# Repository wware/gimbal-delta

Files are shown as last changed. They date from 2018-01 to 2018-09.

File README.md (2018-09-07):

# Gimbal delta printer/CNC

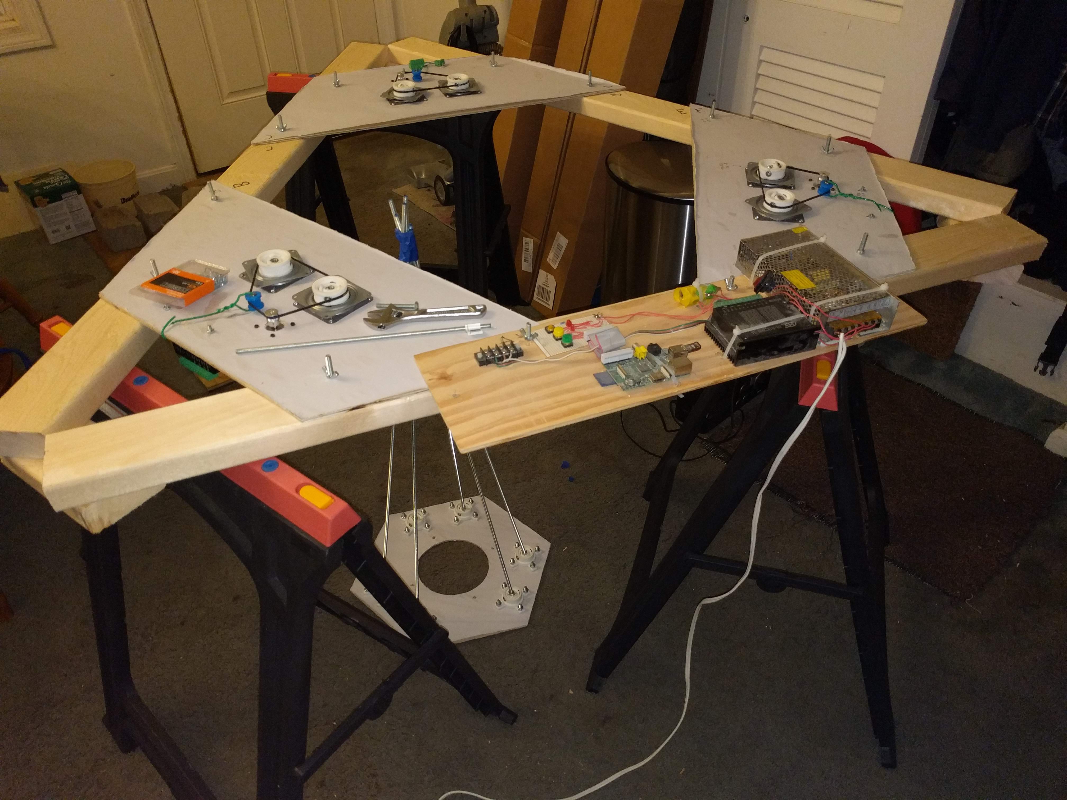
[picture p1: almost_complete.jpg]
Picture of gadget


The fundamental part of the gimbal delta printer is a
[2-axis gimbal](https://github.com/wware/gimbal-delta/blob/master/gimbal1.stl)
holding a nut that takes a 1/4"-20 threaded rod. Each gimbal nut requires
four [684ZZ bearings](https://www.amazon.com/Bearing-684ZZ-4x9-Shielded-4x9x4/dp/B002BBKI7Q).
If you have four gimbal nuts, two mounted to one surface and two mounted
to another, you can have parallel arms as they are used in a
[Rostock delta printer](http://reprap.org/wiki/Delta_geometry) to keep the
tool mount platform horizontal.

So you have
[three pairs of arms](https://github.com/wware/gimbal-delta/blob/master/machine.stl)
like a Rostock, but instead of moving the upper ends of the arms up and down on linear
rails, you shorten and lengthen the three arm pairs. The gimbal nuts on the
tool mount platform are not allowed to rotate, and the threaded rods are epoxied
into their nuts, again to prevent rotation. The gimbal nuts on the printer frame,
at the upper ends of the arm pairs, are driven by a
[GT2 timing belt](http://sdp-si.com/products/timing-belts/gt2.php) to turn in
synchrony, maintaining the parallel-ness of the arm pairs. The belt for each pair
is driven by a stepper motor.

Put a reasonably flexible connector on the tool mount platform, and it will accommodate
a [router](https://www.amazon.com/Routers/b/ref=dp_bc_4?ie=UTF8&node=552866) or an
[extruder](https://www.matterhackers.com/store/c/HotEnds) or a laser engraver, or maybe
just a marker for plotting.

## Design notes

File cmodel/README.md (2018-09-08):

# Calibration model

This is a mathematical model for calibrating the gimbal delta machine. The hope is to get fairly
high positional precision, hopefully a millimeter or better.

The pairs of threaded rods can be modeled as two points, and one of those points can be the tooltip.
Applying that to all three pairs, we have an inverted tetrahedron whose lower vertex is the tooltip.
The calibration process involves using some kind of least-squares method to find the other three
vertices and the lengths of the edges connecting them to the tooltip vertex.

Logistically, the procedure is to begin with approximate values for all these things that are good
enough to move the tooltip around in predictable directions and distances, and then lower the tooltip
onto several points on a flat surface. The locations of those points are known. Using that knowledge
and the controls we used to position the tooltip, we should be able to figure out more accurate
values.

We want to find three lengths and three points, or a total of 12 scalars, so we'll need at least 12
points on our reference surface.

Let's assume that we have nominal rod lengths and our controls are deltas from those nominal lengths.
Let those lengths be La, Lb, and Lc, and the tops of those rods are the points (xa, ya, za),
(xb, yb, zb), and (xc, yc, zc) respectively. The length deltas can be Da, Db, and Dc.

The forward kinematics problem is to map (Da, Db, Dc) to the position of the tooltip (x, y, z). The
inverse kinematics problem is to map (x, y, z) to (Da, Db, Dc). Surprisingly, the inverse kinematics
problem is easier to solve.

    # Given all our parameters...
    X = np.array((x, y, z))
    A = np.array((xa, ya, za))
    B = np.array((xb, yb, zb))
    C = np.array((xc, yc, zc))
    Da = linalg.norm(A - X) - La
    Db = linalg.norm(B - X) - Lb
    Dc = linalg.norm(C - X) - Lc

To solve the forward kinematics problem, we need to specify (Da, Db, Dc) and then find the vector
X representing the intersection of three spheres. This is [a solved problem](https://stackoverflow.com/questions/1406375).
Given the function defined in the last Stack Overflow answer, we can write

    x, y, z = trilaterate(A, B, C, La + Da, Lb + Db, Lc + Dc)

Gee, that was easier than I expected. OK, on to formulating the least-squares method.

Recognize that the values we have for A, B, C, La, Lb, Lc are approximations of values that are
correct but unknown. So we have *our* answer and *the right* answer.

    X~ = F(Da, Db, Dc, A~, B~, C~, La~, Lb~, Lc~)     # parameters known but approximate
    X = F(Da, Db, Dc, A, B, C, La, Lb, Lc)            # paramaters unknown but correct

So set up a square error figure, summed over several (X, D) pairs.

    ErrSq = sum([linalg.norm(X - X~) ** 2 for D in manyDs])
    partial d(ErrSq)/d(param) = 2 * sum([linalg.norm(X - X~) * (dX/dparam) for D in manyDs])

It won't be practical to find a closed form for dX/dparam, so I'll need to iterate a Newton's
method or conjugate-gradient thingy or whatever to solve this. So you have a vector of partial
derivatives

    (dX/dLa, dX/dLb, dX/dLc, dX/dxa, dX/dya, dX/dza, dX/dxb... dX/dzc)

defined for any point in the twelve-space, and you take your D vectors corresponding to the
known reference X points, and you

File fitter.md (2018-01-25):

# What I learned from the fitter piece

The step of 0.25 mm turns out to be too large. The outer dimension
of 9 mm is a bit too snug, but 9.25 mm is way too loose. My guess is
that 9.1 mm might be just right. I think a better step would be 0.05 mm.

Also, there is little need for smaller-than-9-mm sizes. One would be
fine. So my next plan is something like this.

    module ThirdPiece() {
        difference() {
            intersection() {
                ...
            }
            for (n = [-1 : 3])    // note different for-loop limits
                rotate([0, 0, n * 60])
                    rotate([90, 0, 0])
                        translate([0, 0, 0])
                            cylinder(h=60, d=9 + 0.05*n);   // 0.05 mm step
        }
        for (n = [-1 : 3])
            rotate([0, 0, 180 - 30 + n * 60])
                translate([0, R3+5, 0])
                    rotate([-90, 0, 0]) nub(4 + 0.05*n);
    }

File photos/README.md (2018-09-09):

# Photos of the gimbal delta printer/CNC

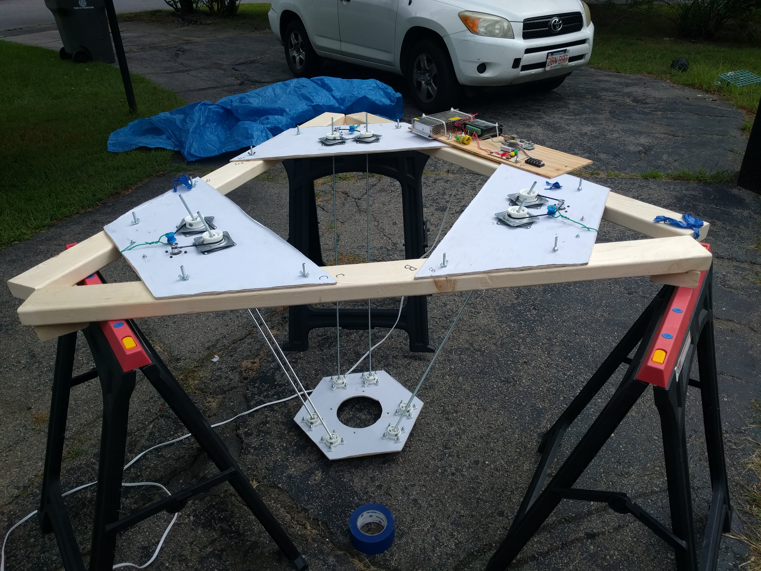
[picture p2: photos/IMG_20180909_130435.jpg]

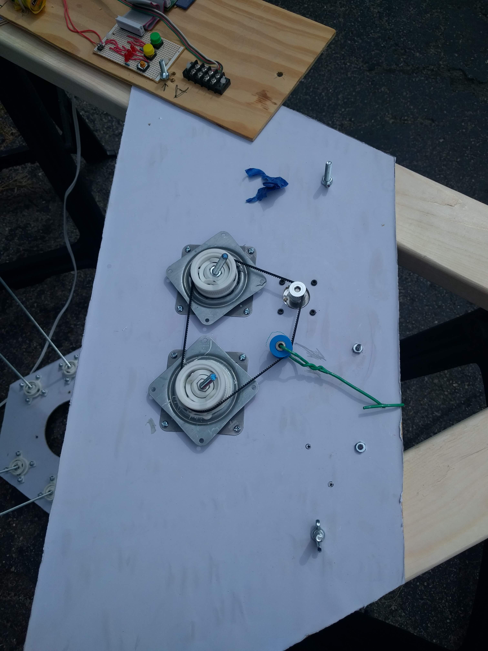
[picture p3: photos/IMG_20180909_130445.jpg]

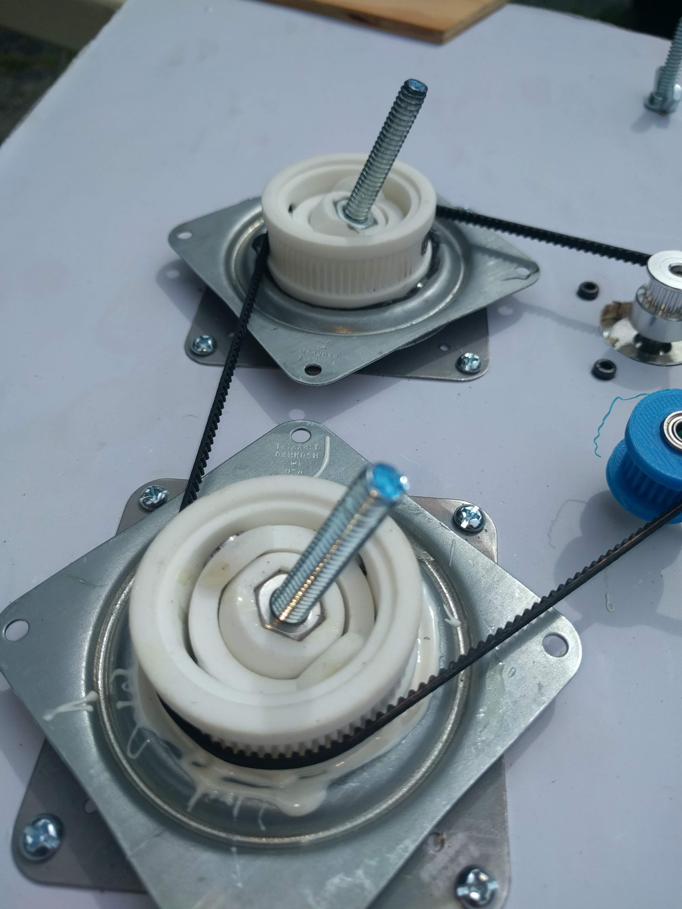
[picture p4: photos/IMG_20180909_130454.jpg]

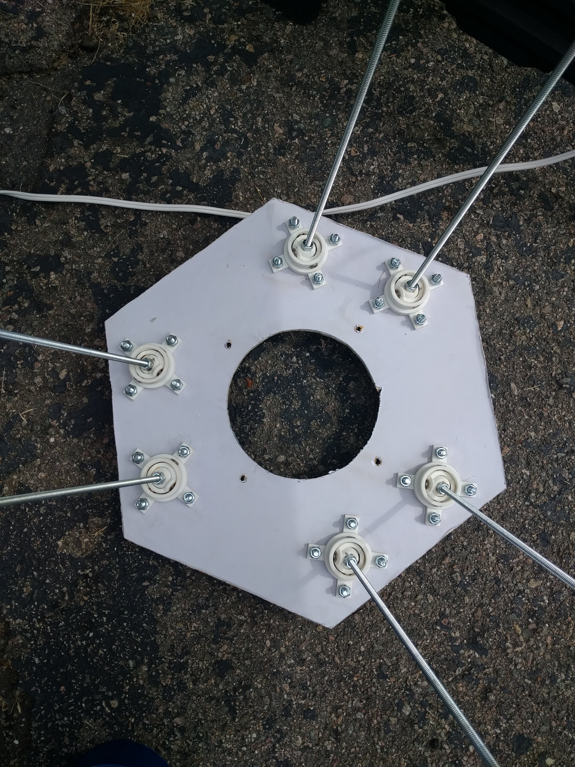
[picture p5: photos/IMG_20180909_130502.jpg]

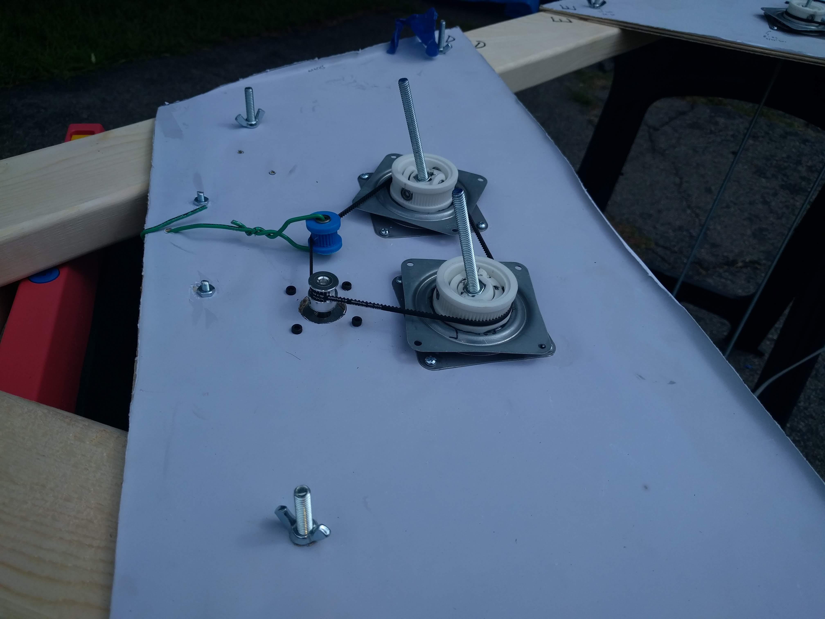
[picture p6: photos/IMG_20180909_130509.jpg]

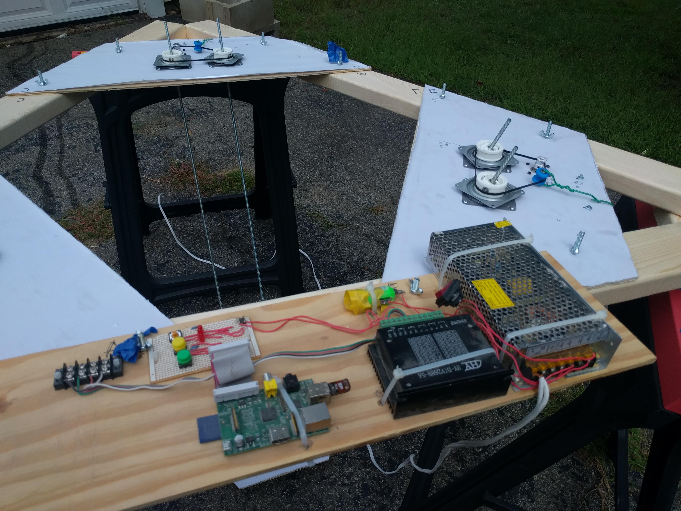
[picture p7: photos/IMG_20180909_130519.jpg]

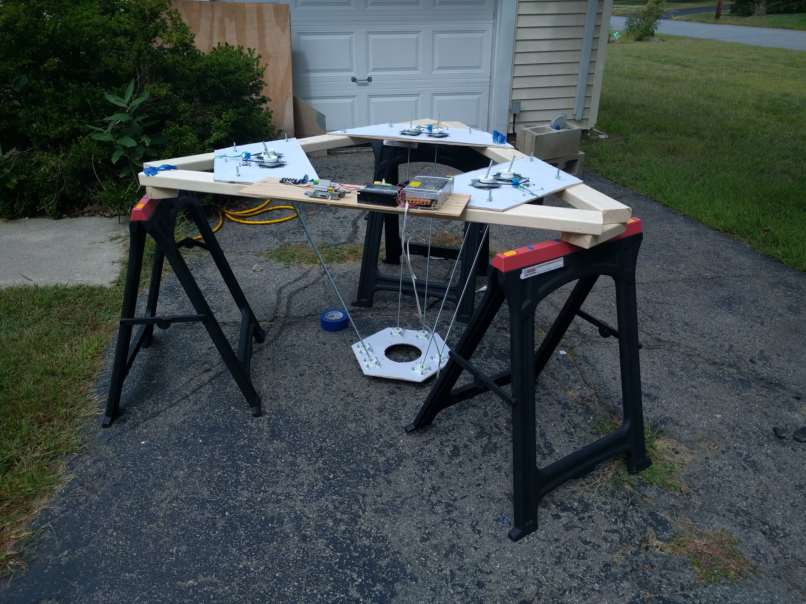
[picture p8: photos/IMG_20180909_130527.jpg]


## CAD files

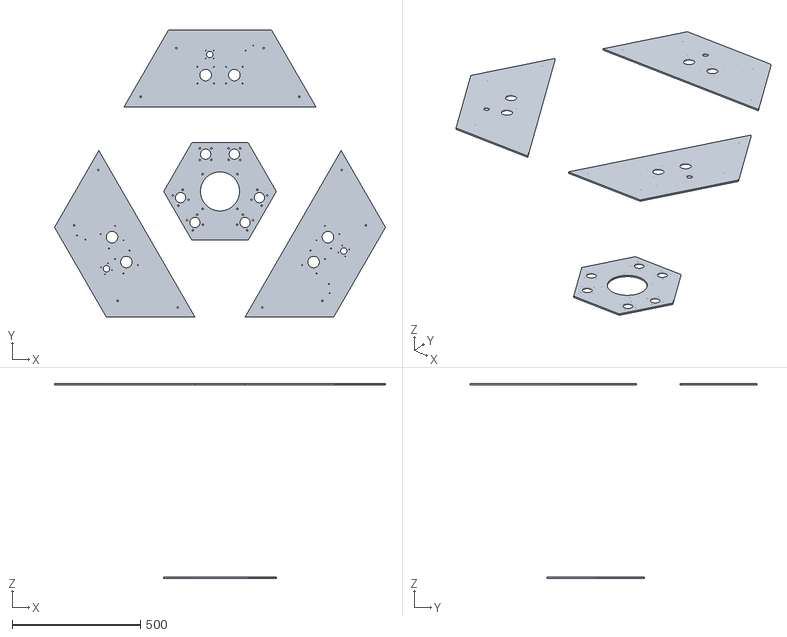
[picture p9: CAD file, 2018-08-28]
machine.stl
1292.8 x 1119.6 x 762.0

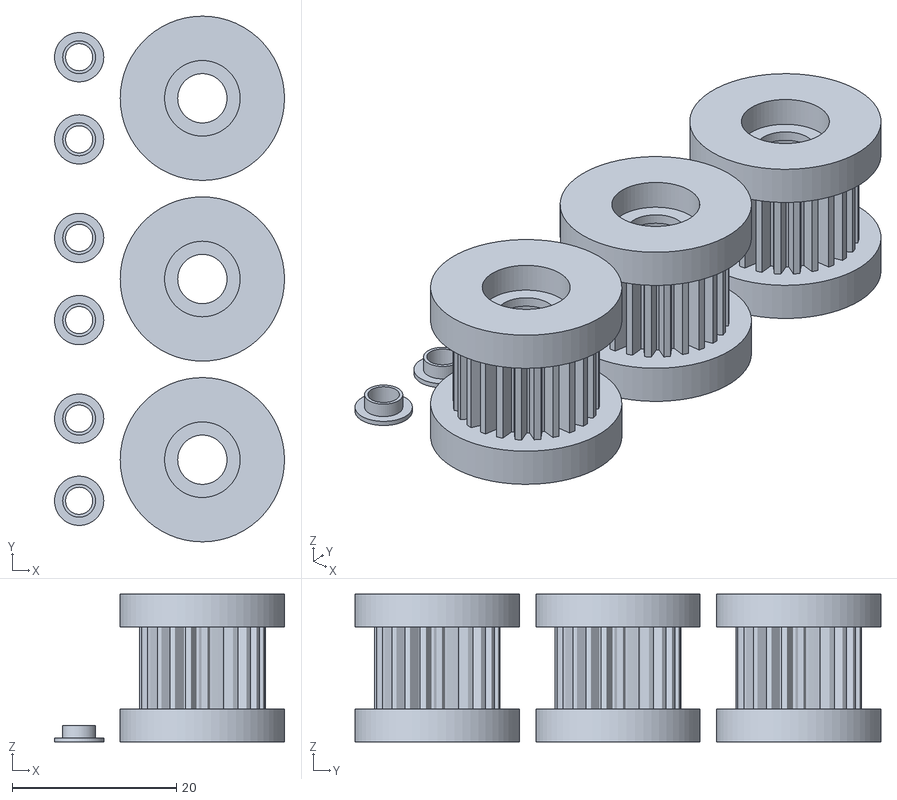
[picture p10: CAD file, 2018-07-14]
tensioner_pieces.stl
28.0 x 64.0 x 18.0

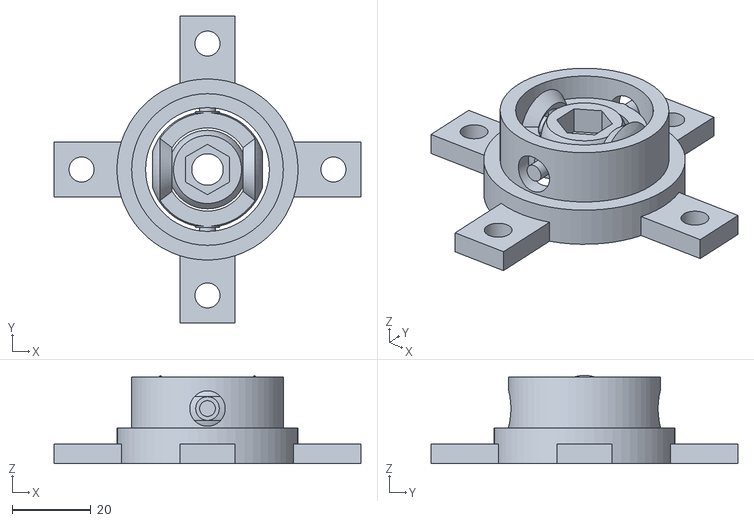
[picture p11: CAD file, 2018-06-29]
fixed_gimbal.stl
78.0 x 78.0 x 22.4

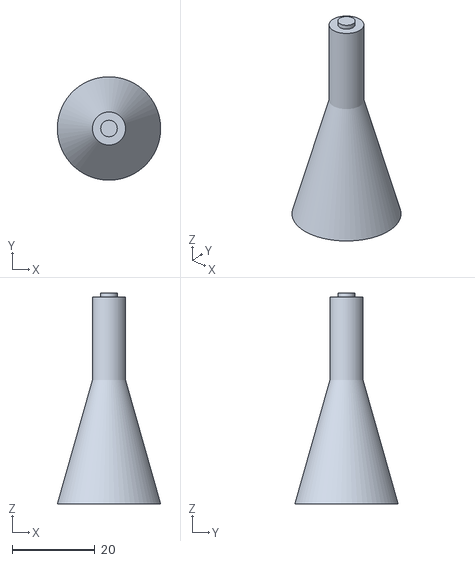
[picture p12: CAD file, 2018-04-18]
tool.stl
25.0 x 25.0 x 51.0

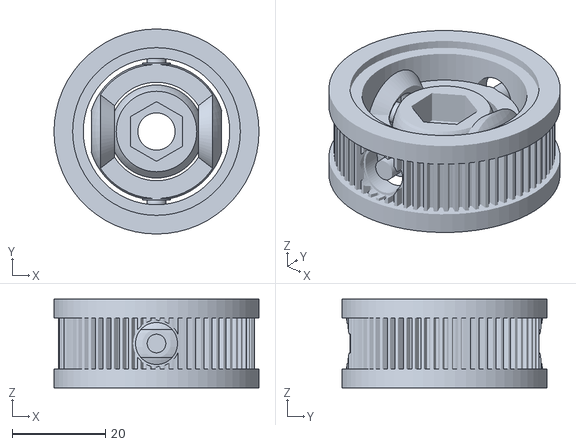
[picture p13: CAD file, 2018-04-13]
rotor.stl
44.0 x 44.0 x 19.0

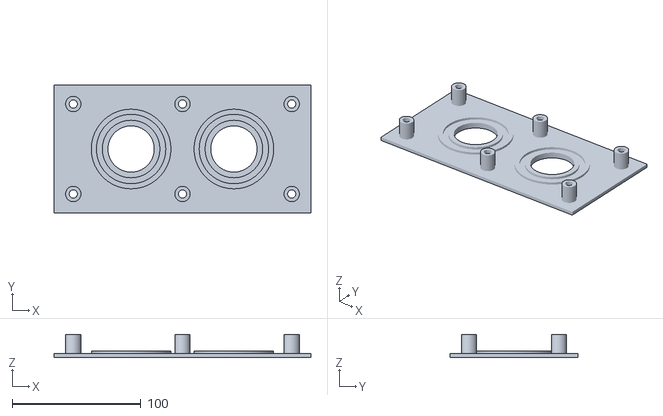
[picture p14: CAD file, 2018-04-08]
baseplate.stl
200.0 x 100.0 x 18.0

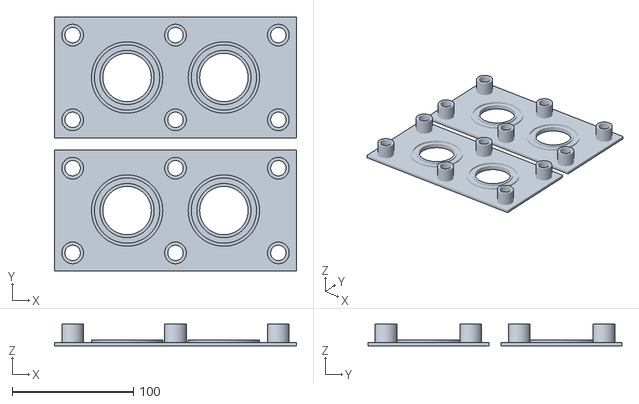
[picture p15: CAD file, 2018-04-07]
two_baseplates.stl
200.0 x 210.0 x 18.0

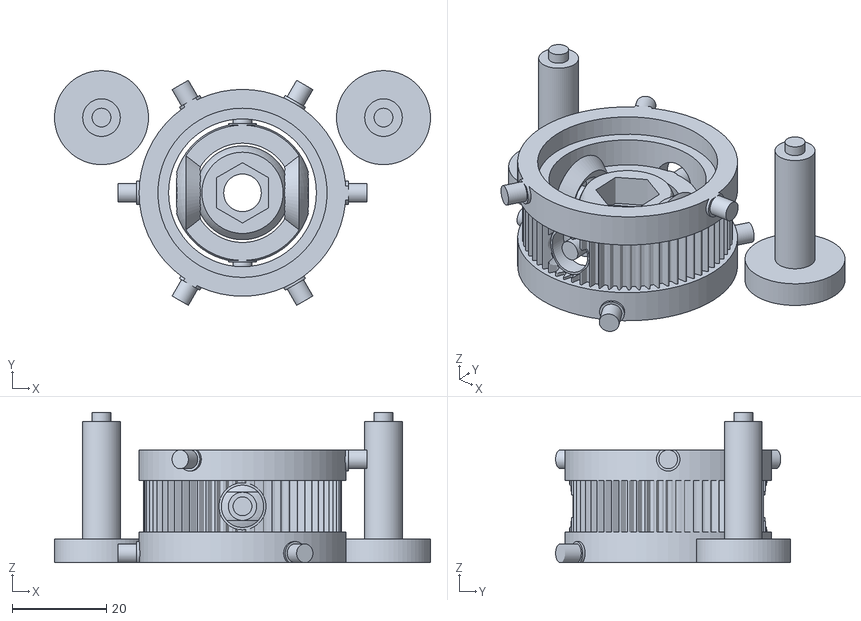
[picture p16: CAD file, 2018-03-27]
rotor2.stl
80.0 x 49.9 x 32.0

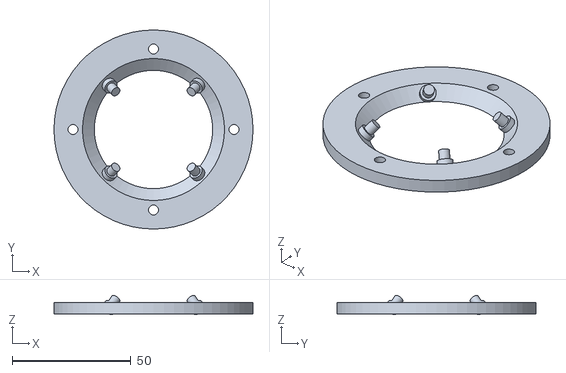
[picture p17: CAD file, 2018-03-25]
altbaseplate.stl
83.8 x 83.8 x 8.07

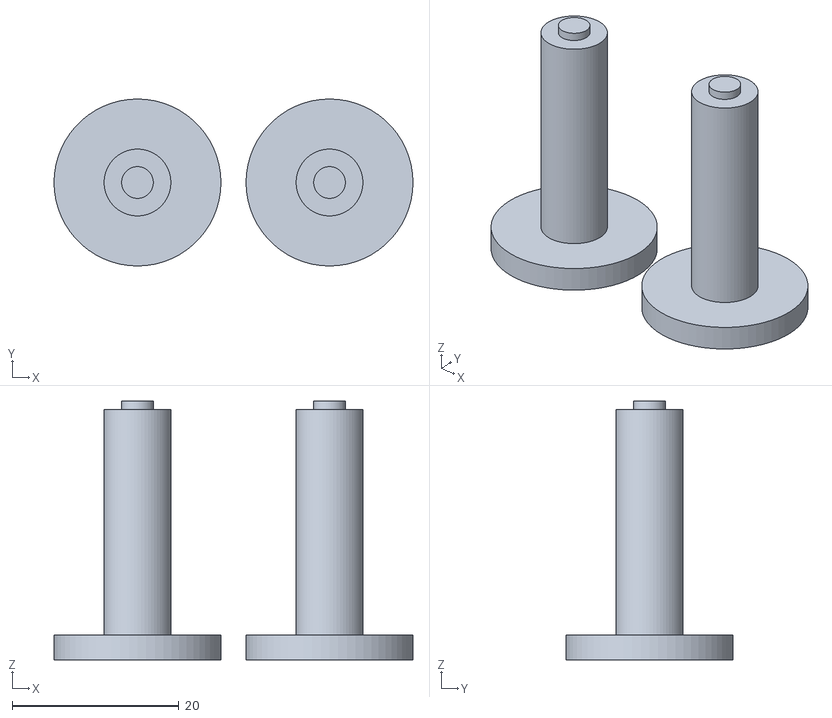
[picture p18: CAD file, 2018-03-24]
bearing_tool.stl
43.0 x 20.0 x 31.0

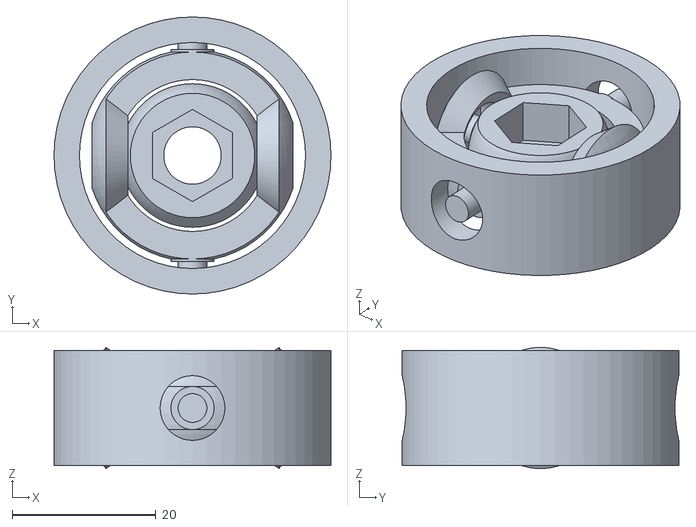
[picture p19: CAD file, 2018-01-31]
gimbal1.stl
38.5 x 38.5 x 16.9

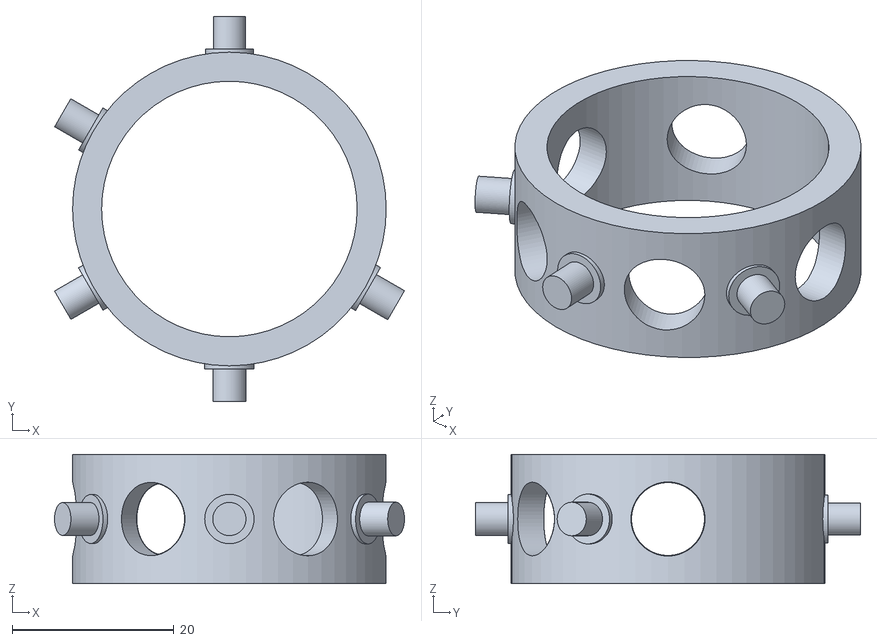
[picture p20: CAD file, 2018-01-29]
fitter.stl
43.2 x 47.6 x 16.0

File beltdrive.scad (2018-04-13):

// $fn = 60;
pi = 3.1415926;

pitch = 2;   // 2GT timing belt

a = 0.4;

module tooth(h) {
    M1 = [[ 1  , a , 0  , 0   ],
           [ 0  , 2 , 0  , 0   ],
           [ 0  , 0 , 1  , 0   ],
           [ 0  , 0 , 0  , 1   ] ] ;
    M2 = [[ 1  , -a , 0  , 0   ],
           [ 0  , 2  , 0  , 0   ],
           [ 0  , 0  , 1  , 0   ],
           [ 0  , 0  , 0  , 1   ] ] ;
    translate([-1, -0.5, -h/2])
        intersection() {
            multmatrix(M1) {
                cube(size=[1.5,1,h]);
            }
            multmatrix(M2) {
                cube(size=[1.5,1,h]);
            }
        }
}

module beltdrive(N, h, w) {
    b = 0.6;
    r = (1 / sin(180 / N)) - 1.5;
    echo(r);
    echo(r-w);
    difference() {
        translate([0, 0, -h/2])
            cylinder(r=r, h=h);
        translate([0, 0, -h/2-1])
            cylinder(r=r-w, h=h+2);
    }
    for (i = [0 : N-1]) {
        rotate(i * 360 / N, [0, 0, 1])
            translate([0, r, 0])
                tooth(h);
    }
}

/* To avoid a "wall too thin" warning from Shapeways, you need the
   outer edge of the tooth to be at least 0.7 mm thick. This requires
   dropping the value of a to 0.4.
 */

// beltdrive(62, 3, 0.6);
// tooth(3);
// translate([-0.6, 1.5, 0]) cube([0.7, 1, 1]);

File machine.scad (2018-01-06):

$fn = 30;
INCH = 25.4;

arm_separation = 70;
driver_width = arm_separation + 60;

// http://reprap.org/wiki/NEMA_17_Stepper_motor
nema17height = 50;    // approximate
nema17width = 42.3;

module GimbalNut() {
    translate([0, 0, -0.01])
        cylinder(r=19.2, h=16);
}

module GimbalNutPair() {
    translate([-.5 * arm_separation, 0, 0])
        GimbalNut();
    translate([.5 * arm_separation, 0, 0])
        GimbalNut();
}

module dewalt660router() {
    // http://www.dewalt.com/products/power-tools/cutout-tools/cutout-tool/dw660
    cylinder(d=3*INCH, h=10*INCH);
    translate([0, 0, -25])
        cylinder(d=15, h=30);
}

hex_diameter = 150;

module ToolMountPlatform() {
    dewalt660router();
    // plywood hexagon
    translate([0, 0, -5])
        linear_extrude(height=5)
            circle(hex_diameter, $fn=6);
    // 3 pairs of gimbal nuts
    for (n = [1 : 3])
        rotate(120 * n, [0, 0, 1])
            translate([0, 100, 0])
                GimbalNutPair();
}

ToolMountPlatform();

module DriverModule() {
    GimbalNutPair();
    // plywood
    translate([-.5*driver_width, -25, -5])
        cube([driver_width, 110, 5]);
    // stepper motor
    translate([-.5*nema17width,
              50 - .5*nema17width,
              -nema17height - 5])
        cube([nema17width, nema17width, nema17height]);
    // stepper motor shaft
    translate([0, 50, 0])
        cylinder(d=0.4*INCH, h=24);
}

// there needs to be a frame to hold the 3 driver modules
for (n = [1 : 3])
    rotate(120 * n, [0, 0, 1])
        translate([0, 380, 600])
            DriverModule();

// threaded rods connecting driver modules to tool mount
for (n = [1 : 3])
    rotate(120 * n, [0, 0, 1])
        for (m = [0 : 1])
            translate([(m - .5) * arm_separation, 100, 8]) {
                rotate(-25, [1, 0, 0])
                    cylinder(d=5, h=36*INCH);
            }

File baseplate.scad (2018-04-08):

$fn=60;

include <gimbal1.scad>;
include <beltdrive.scad>;

GIMBAL_OUTER_DIAMETER = 2 * R5;
GIMBAL_HEIGHT =  thirdHeight;
RING_OFFSET = 4.7;

module gimbal_outline() {
    translate([0, 0, -.5 * GIMBAL_HEIGHT])
    cylinder(d=GIMBAL_OUTER_DIAMETER, h=GIMBAL_HEIGHT);
}

module bearing_684zz() {
    difference() {
        translate([0, 0, -2]) cylinder(h=4, d=9);
        translate([0, 0, -3]) cylinder(h=6, d=4);
    }
}

module bearing_608zz() {
    difference() {
        translate([0, 0, -3.5]) cylinder(h=7, d=22);
        translate([0, 0, -4]) cylinder(h=8, d=8);
    }
}

module bearings() {
    // 6.5 = (9 + 4) / 2, from the bearing
    C = 6.5 / sqrt(2);
    for (i = [0 : 2]) {
        a = 0.5 * GIMBAL_OUTER_DIAMETER + C;
        b = C + RING_OFFSET;
        rotate(30 + 120*i, [0, 0, 1]) {
            translate([a, 0, -b]) rotate(45, [0, 1, 0])
                bearing_684zz();
            translate([a, 0, b]) rotate(45, [0, -1, 0])
                bearing_684zz();
        }
    }
}

module half_shell() {
    w = 23.9;
    intersection() {
        for (j = [0 : 3]) {
            rotate((j+.25)*90, [0, 0, 1])
            translate([w, 0, 0])
                rotate(45, [0, -1, 0]) {
                    h1 = 4;
                    h2 = 2.4;
                    %bearing_684zz();
                    translate([0, 0, -2-0.01])
                        cylinder(d=4, h=4+0.02);
                    translate([0, 0, -(h2+2)])
                        cylinder(d=6, h=h2);
                };
        };
    };
    h = 5;
    difference() {
        k = 12;
        translate([0, 0, -5.1+.01])
            cylinder(r=w+1+k+h, h=h-0.02);
        translate([0, 0, -5.1])
            cylinder(r=w+1+h, h=h);
        for (i = [0 : 3]) {
            rotate(i * 90, [0, 0, 1])
                translate([w+10, 0, -100])
                    // 8-32 machine screw
                    cylinder(d=0.164*25.4, h=200);
        }
    };
    difference() {
        translate([0, 0, -5.1+.01])
            cylinder(r=w+1+h, h=h-0.02);
        translate([0, 0, -5.1])
            cylinder(r1=w+1, r2=w+1+h, h=h);
    };
};


module post() {
    extra = 2;
    translate([0, 0, -(2+extra)]) {
        cylinder(d=4, h=4+extra);
        cylinder(d=5, h=extra);
    };
    %bearing_684zz();
};

module post_pair() {
    C = 6.5 / sqrt(2);
    a = 0.5 * GIMBAL_OUTER_DIAMETER + C;
    b = C + RING_OFFSET;
    for (j = [0 : 1]) {
        rotate(j*180, [1, 0, 0])
            translate([0, 0, b]) rotate(45, [0, -1, 0]) {
                translate([0, 0, -6]) cylinder(d=4, h=8);
                translate([0, 0, -6]) cylinder(d=5, h=4);
            }
    }
    translate([-2.5, 0, 0])
        intersection() {
            rotate(45, [0, 1, 0])
                translate([0, -5, 0])
                    cube([20, 10, 12]);
            translate([3.5, -50, -50])
                cube(100, 100, 100);
        }
    translate([7, -5, -15])
        cube([20, 10, 10]);
}

module flat_head_screw_cutout(D, H, L) {
    // https://tinyurl.com/ybmmaz7t - dimensions
    D = 3; H = 1.7; L = 10;  // M3
    translate([0, 0, -(D+H)/2])
        cylinder(d1=0, d2=D+H+2, h=(D+H)/2+1);
    translate([0, 0, -L])
        cylinder(d=D, h=L);
};

module m3_cutout(L) { flat_head_screw_cutout(3, 1.7, L); };
module m4_cutout(L) { flat_head_screw_cutout(4, 2.3, L); };
module m5_cutout(L) { flat_head_screw_cutout(5, 2.8, L); };
module m6_cutout(L) { flat_head_screw_cutout(6, 3.3, L); };

module posts() {
    C = 6.5 / sqrt(2);
    a = 0.5 * GIMBAL_OUTER_DIAMETER + C;
    for (i = [0 : 2])
        rotate(30 + 120*i, [0, 0, 1])
            translate([a, 0, 0])
                post_pair();
    translate([0, 0, -19.99])
    difference() {
        cylinder(h=5, d=103);
        union() {
            translate([0, 0, -1])
                cylinder(h=7, d=65);
            translate([-125, -15, -1])
                cube([250, 1, 7]);
            translate([33, -28, 5])
                m5_cutout(15);
            translate([-33, -28, 5])
                m5_cutout(15);
            translate([42, -3, 5])
                m5_cutout(15);
            translate([-42, -3, 5])
                m5_cutout(15);
            translate([15, 42.5, 5])
                m5_cutout(15);
            translate([-15, 42.5, 5])
                m5_cutout(15);
        };
    };
}

module cylinder_ring(inner, middle, outer) {
    difference() {
        cylinder(d1=outer, d2=middle, h=0.5*(outer-middle));
        translate([0, 0, -1])
        cylinder(d=inner, h=(2+outer-middle));
    }
}

module with_rings() {
    D = 4 * sqrt(2);
    translate([0, 0, RING_OFFSET])
    cylinder_ring(GIMBAL_OUTER_DIAMETER - 0.1,
        GIMBAL_OUTER_DIAMETER,
        GIMBAL_OUTER_DIAMETER + D);

    translate([0, 0, -RING_OFFSET])
    rotate(180, [1, 0, 0])
    cylinder_ring(GIMBAL_OUTER_DIAMETER - 0.1,
        GIMBAL_OUTER_DIAMETER,
        GIMBAL_OUTER_DIAMETER + D);
}

module ring_with_posts(offset) {
    width = 36;
    thickness = 4;
    height = 6.5;
    translate([0, 0, -2])
    difference() {
        cylinder(d=width+2*thickness, h=height);
        translate([0, 0, -0.01])
        cylinder(d=width, h=height+0.02);
    };
    for (i = [0 : 2]) {
        rotate((i+offset)*120, [0,0,1])
            translate([width/2+thickness+2.5, 0, height-4])
            rotate(90, [0,1,0]) post();
    };
};

module full_rotor() {
    a = 7.5;
    intersection() {
        union() {
            translate([0, 0, a])
                ring_with_posts(0);
            translate([0, 0, -a])
                mirror([0,0,1])
                ring_with_posts(1/2);
        };
        translate([0, 0, -12])
            cylinder(h=24, d=100);
    };
    GimbalNut();
    difference() {
        translate([0, 0, -0.05])
        beltdrive(66, 12.1, 0.6);
        rotate(90, [1, 0, 0])
            translate([0, 0, -25])
                cylinder(h=50, d=10);
    }
}

module rotor_cross_section() {
    intersection() {
        full_rotor();
        translate([-500, -500, -1000])
            cube([1000, 1000, 1000]);
    }
}

module all_posts() {
    gap = 85;
    translate([0, -gap/2, 0]) posts();
    translate([0, gap/2, 0]) mirror([0, 1, 0]) posts();
};

module bearing_tool() {
    W = 20;
    L = 30;
    gap = 3;
    cylinder(h=5, d=W);
    cylinder(h=L+2, d=4);
    cylinder(h=L, d=8);
};

if (0) {
    gap = 85;
    %translate([0, -gap/2, 0]) full_rotor();
    %translate([0, -gap/2, 0]) bearings();
    %translate([0, gap/2, 0]) full_rotor();
    %translate([0, gap/2, 0]) mirror([0, 1, 0]) bearings();
    all_posts();
}
if (0) {
    // post_pair();
    half_shell();
    %translate([0, 0, -9.3]) full_rotor();
    translate([0, 0, -18.55])
        rotate(180, [0, 1, 0])
            half_shell();
}
if (0) {
    p = 25;
    full_rotor();
    if (0) {
        %cylinder(r1=0, r2=p, h=p);
        %rotate(180, [1,0,0]) cylinder(r1=0, r2=p, h=p);
    }/*
    translate([30, 16, -12])
        bearing_tool();
    translate([-30, 16, -12])
        bearing_tool();*/
}
//post();

module track() {
    difference() {
        translate([0, 0, -1]) cylinder(h=3, r=31);
        translate([0, 0, -1.1]) cylinder(h=3.2, r=27);
    };
    difference() {
        translate([0, 0, -1]) cylinder(h=3, r=22.4);
        translate([0, 0, -1.1]) cylinder(h=3.2, r=18);
    };
};

module baseplate() {
    a = 40;
    u = 85;
    v = 35;
    translate([-a, 0, 0]) track();
    translate([a, 0, 0]) track();
    difference() {
        translate([-100, -50, -3])
            cube([200, 100, 3]);
        translate([-a, 0, -5])
            cylinder(r=18, h=10);
        translate([a, 0, -5])
            cylinder(r=18, h=10);
        for (i = [0 : 1]) {
            for (j = [0 : 1]) {
                translate([(2*i-1) * u, (2*j-1) * v, 0]) {
                    translate([0, 0, -5])
                        cylinder(d=6.35, h=10);
                };
            };
        };
        for (j = [0 : 1]) {
            translate([0, (2*j-1) * v, 0]) {
                translate([0, 0, -5])
                    cylinder(d=6.35, h=10);
            };
        };
    };
    for (i = [0 : 1]) {
        for (j = [0 : 1]) {
            translate([(2*i-1) * u, (2*j-1) * v, 0]) {
                difference() {
                    cylinder(d=12, h=15);
                    translate([0, 0, -0.1])
                        cylinder(d=6.35, h=15.2);
                };
            };
        };
    };
    for (j = [0 : 1]) {
        translate([0, (2*j-1) * v, 0]) {
            difference() {
                cylinder(d=12, h=15);
                translate([0, 0, -0.1])
                    cylinder(d=6.35, h=15.2);
            };
        };
    };
};

if (0) {
    translate([0, 0, -15]) {
        %translate([40, 0, 15.5]) {
            full_rotor();
        };
        %translate([-40, 0, 15.5]) {
            full_rotor();
        };
        baseplate();
        translate([0, 0, 30])
            rotate(180, [1, 0, 0])
                baseplate();
    };
}

baseplate();

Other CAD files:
bearing_tool.scad
fitter.scad
gimbal1.scad
rotor.scad
tool.scad

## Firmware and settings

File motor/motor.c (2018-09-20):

#include <unistd.h>
#include <stdlib.h>
#include <stdio.h>
#include <time.h>
#ifdef RASPBERRY_PI
#include <bcm2835.h>
#else
#include "sim_bcm2835.h"
#endif

#define PULA    21
#define DIRA    20
#define ENAA    16

#define PULB    13
#define DIRB    19
#define ENAB    26

#define PULC    12
#define DIRC    25
#define ENAC    24

#define MAX(x,y)  (((x) > (y)) ? (x) : (y))
#define ABS(x)    MAX(x, -(x))

#define MODULO   100000

// PERIOD is in nanoseconds
#define PERIOD   100000L

struct pinstruct {
    int phase;
    int state;
    int pin;
};

static struct pinstruct astruct = { 0, 0, PULA };
static struct pinstruct bstruct = { 0, 0, PULB };
static struct pinstruct cstruct = { 0, 0, PULC };
static int init_done = 0;

void process_pin(struct pinstruct *pstr, int value)
{
    pstr->phase += value;
    if (pstr->phase > MODULO) {
        bcm2835_gpio_write(pstr->pin, pstr->state ? HIGH : LOW);
        pstr->state = !pstr->state;
        pstr->phase %= MODULO;
    }
}

int run_motors(int avalue, int bvalue, int cvalue, int usecs, int enable_debug)
{
    int iter;
    struct timespec ts = {0};

    ts.tv_sec = 0;
    ts.tv_nsec = PERIOD;

    if (enable_debug)
        bcm2835_set_debug(1);

    if (!init_done) {
        if (!bcm2835_init())
            return 1;
        init_done = 1;
    }

    bcm2835_gpio_fsel(PULA, BCM2835_GPIO_FSEL_OUTP);
    bcm2835_gpio_fsel(DIRA, BCM2835_GPIO_FSEL_OUTP);
    bcm2835_gpio_fsel(ENAA, BCM2835_GPIO_FSEL_OUTP);

    bcm2835_gpio_fsel(PULB, BCM2835_GPIO_FSEL_OUTP);
    bcm2835_gpio_fsel(DIRB, BCM2835_GPIO_FSEL_OUTP);
    bcm2835_gpio_fsel(ENAB, BCM2835_GPIO_FSEL_OUTP);

    bcm2835_gpio_fsel(PULC, BCM2835_GPIO_FSEL_OUTP);
    bcm2835_gpio_fsel(DIRC, BCM2835_GPIO_FSEL_OUTP);
    bcm2835_gpio_fsel(ENAC, BCM2835_GPIO_FSEL_OUTP);

    bcm2835_gpio_write(ENAA, HIGH);
    bcm2835_gpio_write(DIRA, (avalue < 0) ? HIGH : LOW);
    avalue = ABS(avalue);

    bcm2835_gpio_write(ENAB, HIGH);
    bcm2835_gpio_write(DIRB, (bvalue < 0) ? HIGH : LOW);
    bvalue = ABS(bvalue);

    bcm2835_gpio_write(ENAC, HIGH);
    bcm2835_gpio_write(DIRC, (cvalue < 0) ? HIGH : LOW);
    cvalue = ABS(cvalue);

    for (iter = 0; iter < usecs; iter++) {
        if (enable_debug)
            printf("%d %d %d %d\n", iter, astruct.phase, bstruct.phase, cstruct.phase);
	process_pin(&astruct, avalue);
	process_pin(&bstruct, bvalue);
	process_pin(&cstruct, cvalue);
        nanosleep(&ts, (struct timespec *) NULL);
    }

    bcm2835_gpio_write(ENAA, LOW);
    bcm2835_gpio_write(ENAB, LOW);
    bcm2835_gpio_write(ENAC, LOW);

    return 0;
}

#ifdef MOTORMAIN
const char *helpstring = "MODULO=%d PERIOD=%d\n"
"  Example usage: %s -D 10000 -c 45000\n"
"Command line options\n"
"    -a <n>   rate multiple of the A motor, positive up, negative down\n"
"    -b <n>   rate multiple of the B motor, positive up, negative down\n"
"    -c <n>   rate multiple of the C motor, positive up, negative down\n"
"    -D <n>   duration\n"
"    -h,-?    help\n";

int main(int argc, char **argv)
{
    int c, debugflag = 0, duration = 300;
    int avalue = 0, bvalue = 0, cvalue = 0;

    while ((c = getopt (argc, argv, "?ha:b:c:D:d")) != -1)
        switch (c) {
            case 'h':
            case '?':
                printf(helpstring, MODULO, PERIOD, argv[0]);
                return 0;
            case 'a':
                avalue = atoi(optarg);
                break;
            case 'b':
                bvalue = atoi(optarg);
                break;
            case 'c':
                cvalue = atoi(optarg);
                break;
            case 'D':
                duration = atoi(optarg);
                break;
            case 'd':
                debugflag = 1;
                break;
            default:
                abort();
        }

    return run_motors(avalue, bvalue, cvalue, duration, debugflag);
}
#endif

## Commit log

2018-01-04 an STL file
    [gimbal1.stl]
2018-01-04 Better range of motion
    [gimbal1.scad, gimbal1.stl]
2018-01-04 The entire machine in outline.
    [machine.scad, machine.stl]
2018-01-05 Corrections in machine overview
    [machine.scad, machine.stl]
2018-01-06 more realistic sizing
    [machine.scad, machine.stl]
2018-01-09 Clean up gimbal design, bump up wiggle room.
    [gimbal1.scad, gimbal1.stl]
2018-01-17 Different sizes to fit the bearing.
    [fitter.scad, fitter.stl]
2018-01-29 A better fitter piece.
    [fitter.scad, fitter.stl]
2018-01-31 Try an outer diameter of 9.1 mm, inner 4 mm
    [gimbal1.scad, gimbal1.stl]
2018-02-02 Rotor for driving a gimbal nut.
    [rotor.scad, rotor.stl]
2018-02-13 Rework the rotor.
    [rotor.scad, rotor.stl]
2018-02-24 Add a beltdrive
    [beltdrive.scad]
2018-02-24 Put a bunch of pieces together.
    [beltdrive.scad, rotor.scad]
2018-03-06 Redesign the timing belt teeth.
    [beltdrive.scad, gimbal1.scad, rotor.scad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]
2018-03-06 Try to fix Shapeways walls-too-thin warning.
    [beltdrive.scad, rotor.stl]
2018-03-24 Bearing insertion tool
    [bearing_tool.scad, bearing_tool.stl]
2018-03-24 Baseplate and stl
    [baseplate.stl, rotor.scad]
2018-03-25 Alternative to baseplate with STL
    [altbaseplate.stl, rotor.scad]
2018-03-25 Try four bearings to support, with STL
    [altbaseplate.stl, rotor.scad]
2018-03-26 new rotor design
    [rotor.scad]
2018-03-27 more work
    [rotor.scad, rotor2.stl]
2018-04-07 Baseplates with circular tracks
    [baseplate.scad, two_baseplates.stl]
2018-04-07 more baseplate work
    [baseplate.scad, baseplate.stl]
2018-04-08 diameter not radius
    [baseplate.scad, baseplate.stl]
2018-04-08 Use a lazy susan bearing (https://amzn.to/2JtA3F3)
    [rotor.scad]
2018-04-13 Fix wall-too-thin warning from Shapeways.
    [beltdrive.scad, rotor.scad, rotor.stl]
2018-04-18 Better insertion tool, I hope.
    [tool.scad, tool.stl]
2018-06-05 here's a driver design (start of one), and move rotor up a little
    [driver.scad, rotor.scad]
2018-06-29 the fixed gimbal design
    [fixed_gimbal.stl, rotor.scad]
2018-06-29 replace driver.scad with better
    [driver.scad, rotor.scad]
2018-06-29 Add a STL file for the driver module.
2018-07-06 more work on driver module
    [rotor.scad]
2018-07-10 more tensioner work
    [rotor.scad]
2018-07-26 Lots of progress
    [rotor.scad]
2018-07-26 simplify a bit
    [rotor.scad]
2018-07-26 more simplifications
    [rotor.scad]
2018-07-27 Generate SVG for PDF for plywood.
    [rotor.scad]
2018-08-19 Make tool platform bigger, build triangle of drivers.
    [rotor.scad]
2018-08-20 whole thing
    [rotor.scad]
2018-08-27 Threaded rod at controlled angle.
    [rotor.scad]
2018-08-28 more updates to machine.stl
    [rotor.scad]
2018-08-31 noodling with dimensions
    [rotor.scad]
2018-09-08 start thinking about calibration
2018-09-13 preliminary motor control software
2018-09-19 more work on motor.c
